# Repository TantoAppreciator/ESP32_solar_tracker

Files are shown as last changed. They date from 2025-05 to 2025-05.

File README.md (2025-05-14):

# ESP32_solar_tracker
Задача: создать устройство, которое при подключении к интернету управляет двумя шаговыми моторами и тем самым направляет импровизированную панель (макет) в сторону солнца.

Решение: горизонтальный мотор крепится на подставке к плате, сделанную ЛУТом. "Ноль" азимута определяется по датичку холла. Определённой стороной нужно выставить устройство на север вручную. Аналогичным способом определяется "ноль" вертикального мотора. Индикатором состояния служит светодиод. Микроконтроллер при подключении к интернету берёт координаты с помощью ip и парсит их с сайта. Время аналогично передаётся по интернету. После необходимых вычислений панель позиционируется в сторону солнца и каждые 10 минут микроконтроллер уточняет координаты и соответственно регулирует положение макета.

Компоненты: ESP32, порт USB, плата, 2 шаговых мотора 28BYJ-48, 2 драйвера к ним, провода, напечатанная подставка, мачта, макет панели, 2 датчика холла, 2 магнита.

Инструменты: solidworks, kicad, шестигранник, паяльник.

Трудности: перекрутка проводов, небольшой люфт, крепление датчиков холла. В основном решены.





https://github.com/user-attachments/assets/a26288a7-7bdc-401f-adb5-59ec2774fa0a

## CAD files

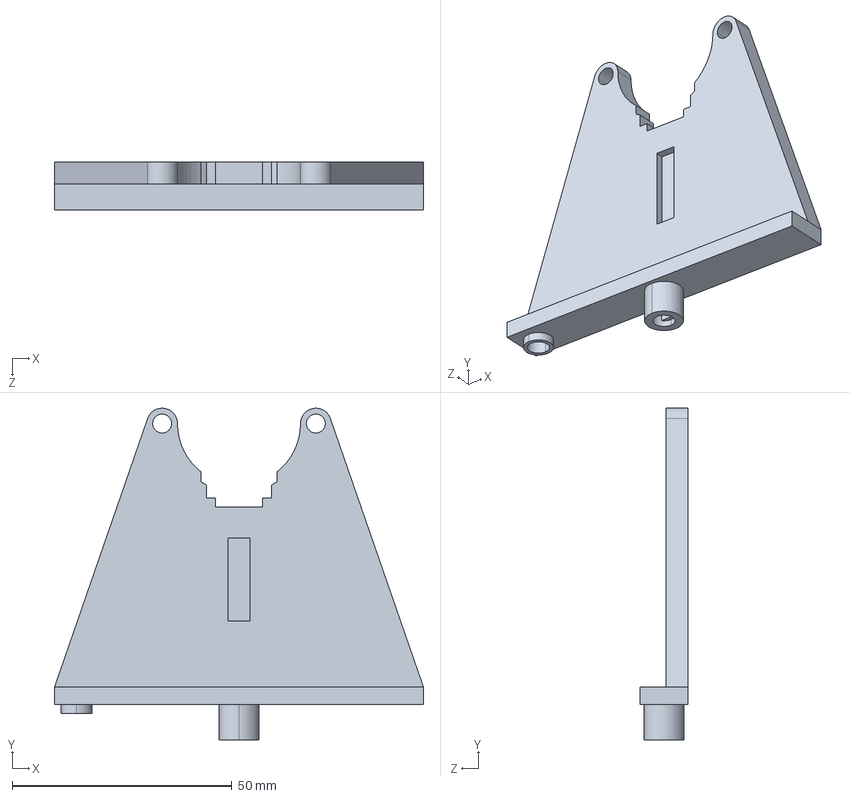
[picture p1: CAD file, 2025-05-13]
3d models/Вертикальный держатель.STEP
84.0 x 75.5 x 11.0 mm

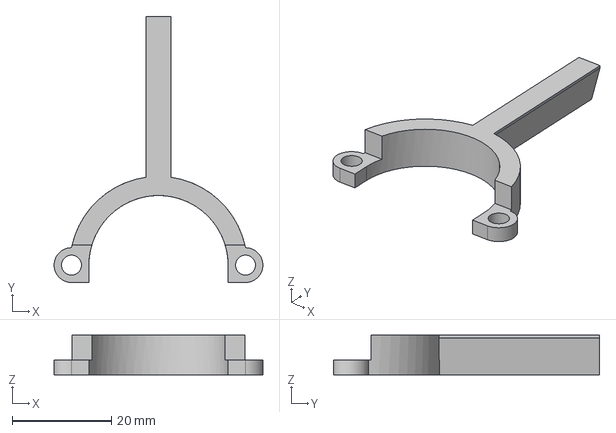
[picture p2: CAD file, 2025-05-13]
3d models/Hall sensor mount arm.stp
42.0 x 53.5 x 8.00 mm

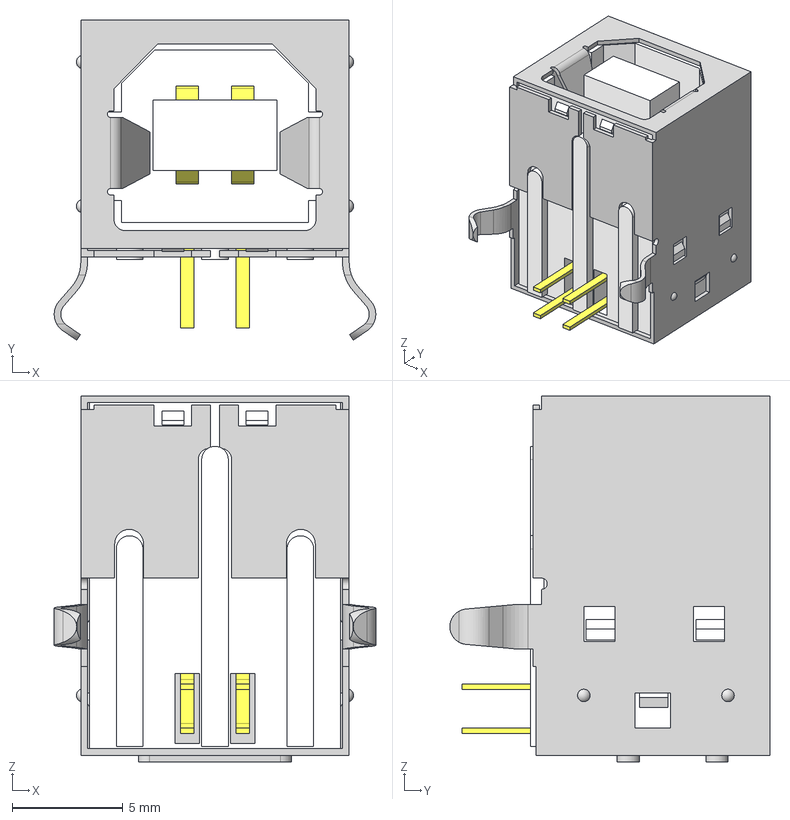
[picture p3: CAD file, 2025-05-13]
3d models/USB-B-S-F-W-TH.stp
14.5 x 14.4 x 16.5 mm
USB-B-S-TH_S
USB-B-S-W-TH_B
USB-B-S-TH_P

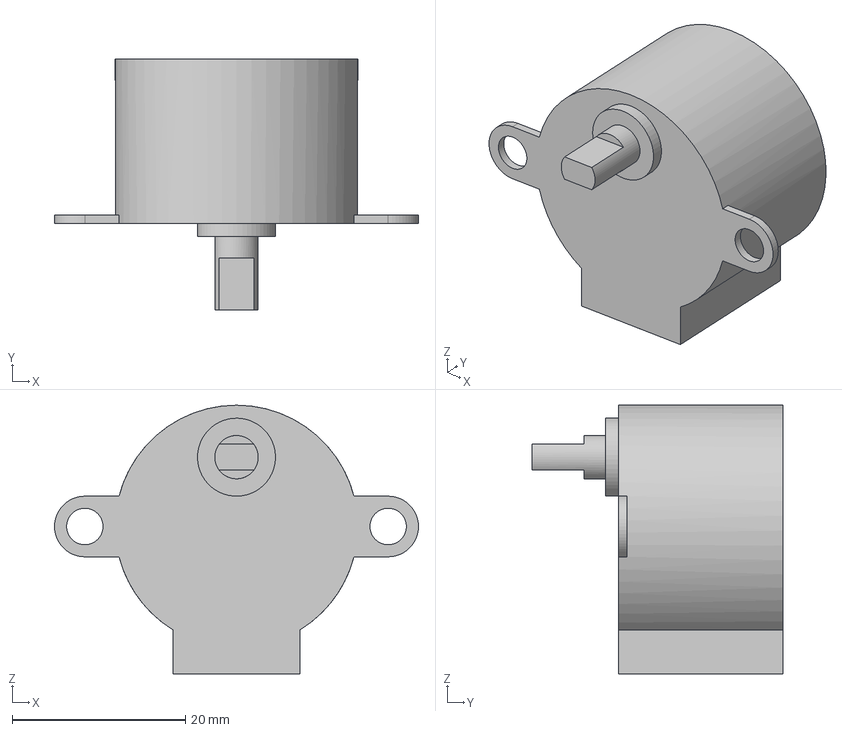
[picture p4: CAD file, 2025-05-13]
3d models/28byj-48.stp
42.0 x 29.0 x 31.0 mm

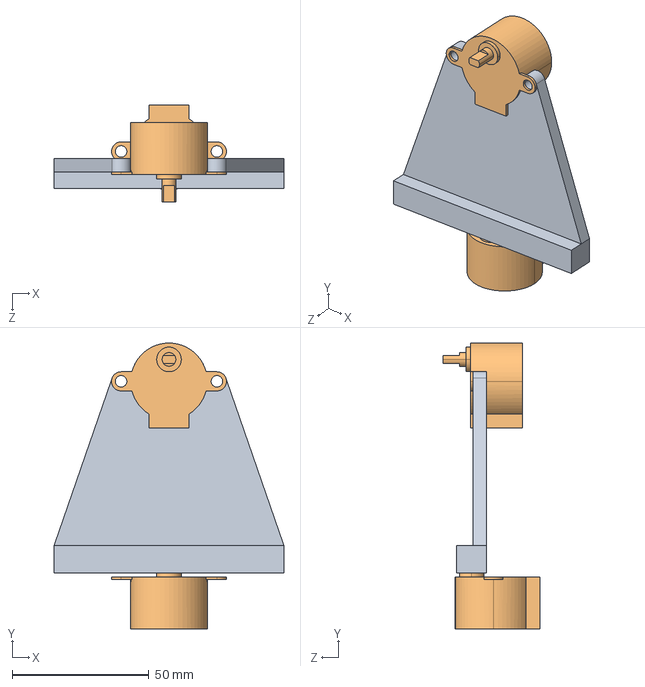
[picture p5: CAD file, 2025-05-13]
3d models/Вертикальная_подставка_с_двигателями.STEP
84.0 x 104.5 x 35.5 mm
Âåðòèêàëüíûé äåðæàòåëü
Äâèãàòåëü x 2

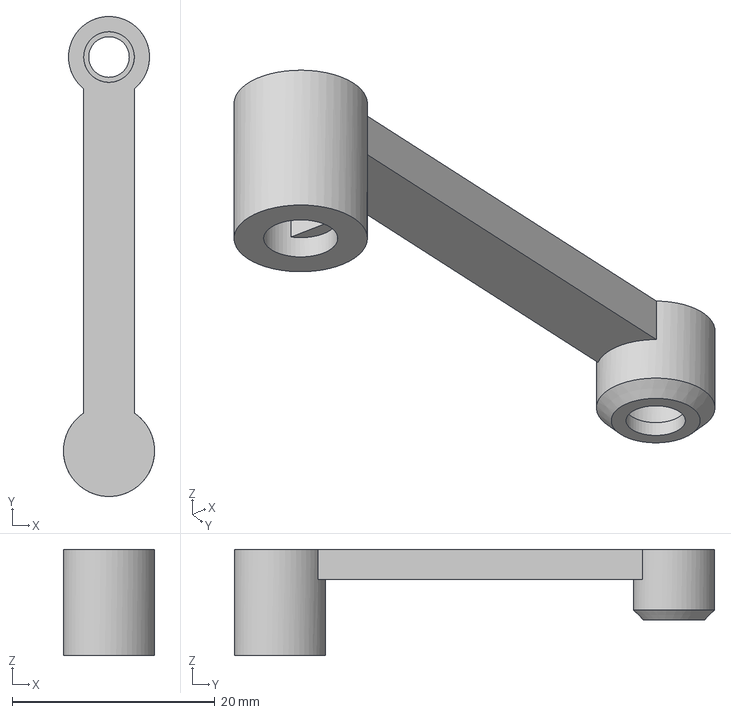
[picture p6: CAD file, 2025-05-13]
3d models/Horizontal drive magnet mount.stp
9.00 x 47.4 x 10.5 mm

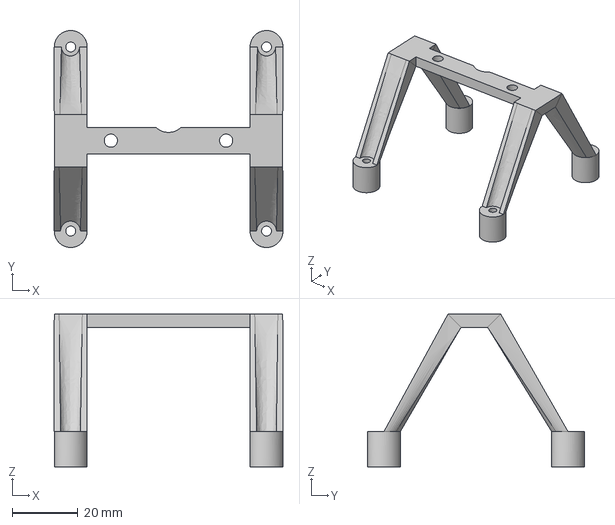
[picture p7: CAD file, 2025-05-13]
3d models/Motor Mount.stp
69.5 x 65.9 x 46.4 mm

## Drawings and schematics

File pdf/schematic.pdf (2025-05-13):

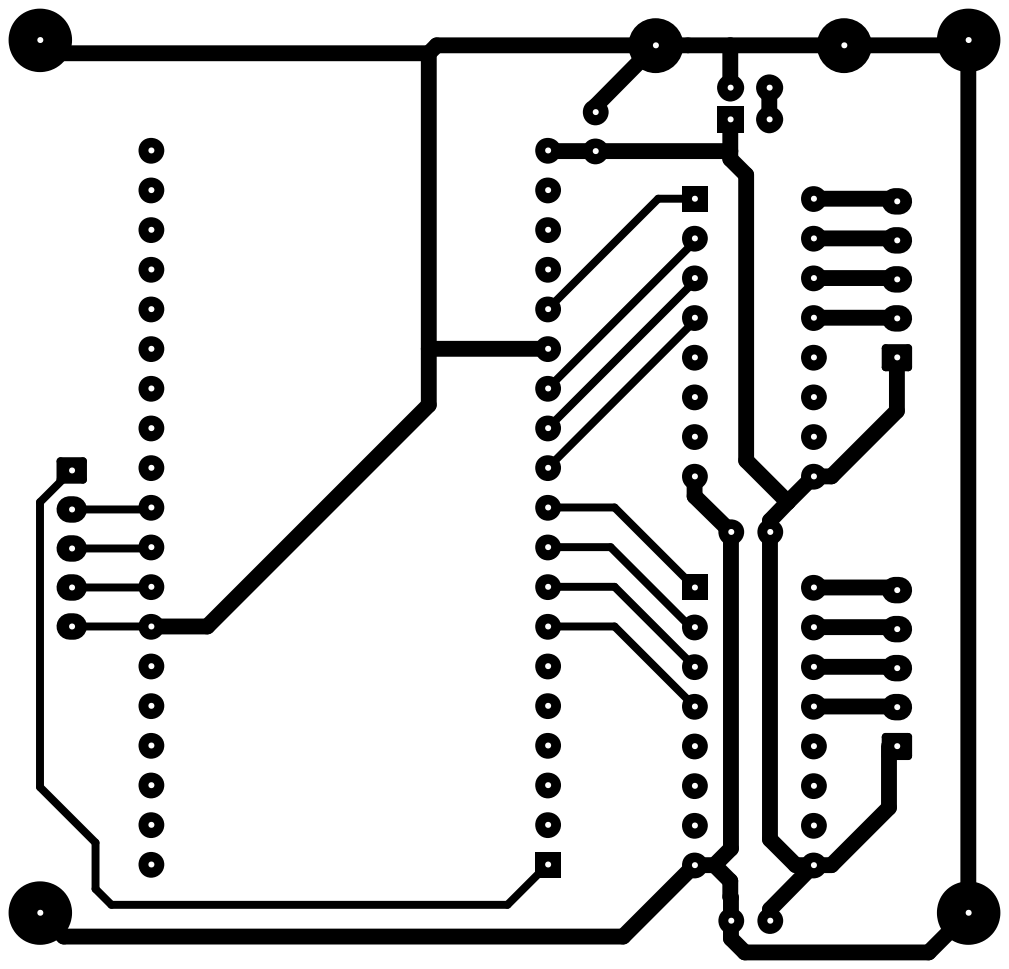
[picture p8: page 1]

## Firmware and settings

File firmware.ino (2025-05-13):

/*

ESP32 based solar tracker
setup assumes "zero" (hall sensor) position facing NORTH
28BYJ-48 electric motors used for azimuth and elevation tracking
Current location calculated from IP address
*/

//motor control declarations
#include <AccelStepper.h>

#define FULLSTEP 4      //from motor specs
#define REV 2048        //steps for full revolution from motor specs
#define PIN_AZI_HOME 5  //Hall sensor digital input
#define PIN_ELEV_HOME 19    //\\\\\\\\\\\\\\\\\\\\\\\\\\\\\\\\\\\\\\\\\\\\\\\\\\\\\\\\\\\\\\\\\\\\\\\\\\\\\\\\\\\\\\\\\\\\\\\\\\\\\\\\\\\\\\\\\\\\\\\\\\\\\\\\\\\\\\\\\\\\\\\\\\\\\\\\\\\\\\\\\\\\\\\\\\\\\\\\\\\\\\\\\\\\\\\\\\\\\\\\\\\\\\\\\\\

AccelStepper stepperAzi(FULLSTEP, 13, 14, 12, 27);
AccelStepper stepperElev(FULLSTEP, 26, 33, 25, 32);   //\\\\\\\\\\\\\\\\\\\\\\\\\\\\\\\\\\\\\\\\\\\\\\\\\\\\\\\\\\\\\\\\\\\\\\\\\\\\\\\\\\\\\\\\\\\\\\\\\\\\\\\\\\\\\\\\\\\\\\\\\\\\\\\\\\\\\\\\\\\\\\\\\\\\\\\\\\\\\\\\\\\\\\\\\\\\\\\\\\\\\\\\\\\\\\\\\\\\\\\\\\\\\\\\\\\

//web request declarations
#include <WiFi.h>
#include <time.h>
#include <ArduinoJson.h>
#include <HTTPClient.h>

#define WIFI_SSID "autobra"
#define WIFI_PASSWORD "731731177"  //todo: find a way to avoid hardcoding SSID and password into the chip
#define LOCATION_REQ_ADDR "http://ip-api.com/json/?fields=33579200"
#define NTP_SERVER "pool.ntp.org"

JsonDocument JSONDoc;  //Memory pool for JSON data from ip-api server
struct tm timeinfo;    //time returned from NTP server
time_t utc;            //unix timestamp

//position calculation declarations
#include <SolarCalculator.h>

double lat;
double lon;
double azi;
double elev;

//debug LED declarations
#define PIN_STAT_LED 18
#define WAIT_SHORT 50
#define WAIT_LONG 500

unsigned long prevMillis;
unsigned long currentMillis;

void setup() {
  // Настройка пинов
  pinMode(PIN_AZI_HOME, INPUT_PULLDOWN);
  pinMode(PIN_ELEV_HOME, INPUT_PULLDOWN);
  pinMode(PIN_STAT_LED, OUTPUT);

  // Настройка Serial
  Serial.begin(115200);
  Serial.println("Delay before setup...");
  delay(2000);

  // Настройка шаговых двигателей
  stepperAzi.setMaxSpeed(500);
  stepperAzi.setAcceleration(100);
  stepperAzi.setSpeed(500);

  stepperElev.setMaxSpeed(500);
  stepperElev.setAcceleration(100);
  stepperElev.setSpeed(500);

  // Инициализация переменных
  bool WiFiConnected = false;
  bool stepperAziHome = false;
  bool stepperElevHome = false;

  WiFi.begin(WIFI_SSID, WIFI_PASSWORD);
  Serial.println("Initial setuo...");
  blinkLED(WAIT_SHORT, 1);
  prevMillis = millis();

  // Переменные для мотора азимута
  long initialAziPosition = stepperAzi.currentPosition();
  int aziDirection = 1; // 1 - по часовой, -1 - против часовой
  bool directionChanged = false; // Флаг смены направления

  // Цикл калибровки и подключения к Wi-Fi
  while (!WiFiConnected || !stepperAziHome || !stepperElevHome) {
    currentMillis = millis();

    // Проверка подключения Wi-Fi
    if (WiFi.status() == WL_CONNECTED && !WiFiConnected) {
      WiFiConnected = true;
      Serial.print("[Wi-Fi connected]");
    }

    // Управление мотором азимута
    if (!stepperAziHome) {
      if (digitalRead(PIN_AZI_HOME)) {
        stepperAziHome = true;
        Serial.print("[Azi motor homing complete]");
        stepperAzi.setCurrentPosition(0);
        stepperAzi.disableOutputs();
      } else {
        long stepsMoved = abs(stepperAzi.currentPosition() - initialAziPosition);
        if (stepsMoved >= 1024 && !directionChanged) {
          // Смена направления после 180 градусов (1024 шага)
          aziDirection *= -1;
          initialAziPosition = stepperAzi.currentPosition();
          stepperAzi.setSpeed(500 * aziDirection);
          directionChanged = true;
          Serial.println("[Azi motor changed direction]");
        }
        stepperAzi.runSpeed(); // Продолжаем движение
      }
    }

    // Управление мотором высоты
    if (!stepperElevHome) {
      if (digitalRead(PIN_ELEV_HOME)) {
        stepperElevHome = true;
        Serial.print("[Elev motor homing complete]");
        stepperElev.setCurrentPosition(0);
        stepperElev.disableOutputs();
      } else {
        stepperElev.runSpeed();
      }
    }

    // Индикация процесса
    if (currentMillis - prevMillis > 100) {
      Serial.print("-");
      digitalWrite(PIN_STAT_LED, !digitalRead(PIN_STAT_LED));
      prevMillis = currentMillis;
    }
  }
  Serial.println("");
  digitalWrite(PIN_STAT_LED, LOW);

  // Получение данных о местоположении
  Serial.println("Getting location data...");
  blinkLED(WAIT_SHORT, 2);
  HTTPClient http;
  http.begin(LOCATION_REQ_ADDR);
  int httpCode = http.GET();
  String payload;

  if (httpCode > 0 && httpCode == HTTP_CODE_OK) {
    payload = http.getString();
    Serial.println(payload);
  } else {
    Serial.printf("[HTTP GET failed...: %s\n", http.errorToString(httpCode).c_str());
  }
  http.end();

  // Разбор JSON для получения координат
  DeserializationError error = deserializeJson(JSONDoc, payload);
  if (!error) {
    lat = JSONDoc["lat"];
    lon = JSONDoc["lon"];
  Serial.printf("JSON parse success: Latitude: %f, longtitude: %f\n", lat, lon);
  } else {
    Serial.println("JSON parse failed.");
  }

  adjustPanel();
  Serial.println("Setup done.");
}

void loop() {
  // put your main code here, to run repeatedly:
  delay(60*10*1000);  //wait 10 minutes
  adjustPanel();
}

void adjustPanel() {
  blinkLED(WAIT_SHORT,5);
  bool timeAcquired = false;

  do{
    Serial.println("Caution! Elevation below zero");
    timeAcquired = false;
  //get time information
  Serial.println("Getting time data...");
  while (!timeAcquired) {
    configTime(0, 0, NTP_SERVER);
    if (!getLocalTime(&timeinfo)) {
      Serial.println("Failed to acquire time data! Retrying after some time...");
      blinkLED(WAIT_LONG,4);
      //reset to defaults somehow
    } else {
      Serial.print("Time data acquired: ");
      Serial.println(&timeinfo, "%A, %B %d %Y %H:%M:%S");
      utc = mktime(&timeinfo);
      Serial.print("Time data Unix timestamp: ");
      Serial.println(utc);
      timeAcquired = true;
    }
  }
  calcHorizontalCoordinates(utc, lat, lon, azi, elev);
  Serial.printf("Coordinates calculated: azimuth: %f, elevation: %f...\n", azi, elev);
  if (elev < 0)
    delay(60*10*1000);
  } while (elev < 0);

  Serial.println("Rotating platform into position...");

    //rotating Azi motor
  stepperAzi.enableOutputs();
    Serial.println(azi);
  double bufazi;
  if(azi > 180)
  {
    bufazi = 360 - azi;
  }
  if(0 <= azi && azi <= 180){
    bufazi = -azi;
  }

  stepperAzi.moveTo(convertDegToRev(bufazi));

  while (stepperAzi.distanceToGo() != 0) {
      stepperAzi.run();
  }
  stepperAzi.disableOutputs();
    //rotating Elev motor
  stepperElev.enableOutputs();
  stepperElev.moveTo(convertDegToRev(elev - 90));

  while (stepperElev.distanceToGo() != 0) {
    stepperElev.run();
  }
  stepperElev.disableOutputs();
}

void blinkLED(int msEach, int amtBlinks){
  digitalWrite(PIN_STAT_LED, LOW);
  for (int i = 0; i < (amtBlinks*2); i++){
    digitalWrite(PIN_STAT_LED, !digitalRead(PIN_STAT_LED));
    delay(msEach/2);
  }
}

double convertDegToRev(double deg) {
  //360 degrees = 1 full revolution (REV macro)
  //i.e. 180 degrees = 1/2 turn = REV * 1/2
  //to convert, multiply REV by deg/360
  double revOut = REV * (deg / 360);
  return revOut;
}

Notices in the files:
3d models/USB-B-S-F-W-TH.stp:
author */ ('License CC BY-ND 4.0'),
